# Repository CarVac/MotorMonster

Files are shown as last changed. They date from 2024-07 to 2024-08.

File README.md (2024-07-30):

# MotorMonster

MotorMonster is intended to be a 5x TMC2160 stepper driver board for 3D printers and other applications, that is actually designed to properly drive the optimal currents for high performance NEMA 17 motors: just north of 2.8 amps RMS.

Many existing 3D printer boards use improper sense resistors.
The BTT SKR Pico, for example, has a limit of 1.4 amps RMS due to its high sense resistor values.
Conversely, the BTT Kraken overspecs its currents with extremely low sense resistors, leaving the TMC drivers starved for sense voltage resolution.

Other boards use StepStick drivers for modularity, but those have worse thermal dissipation than integrated drivers.

The goal of this project is to have a focused, single-board solution for high performance motor driving, leaving everything else to be left to a standard 3D printer motherboard.
With 5 drivers, it should be suitable for 4WD CoreXY + an extruder, or cross gantry + an extruder.

You can choose what sense resistors you want to tailor the board to your own needs.

The MCU is an RP2040, which may be a tad bit slow for the very fastest applications but it's a chip I have a lot of experience with, reducing development risk.

# Acknowledgements

The RP2040 and supporting circuitry is based on https://github.com/Armastardo/OpenRectangleTemplate

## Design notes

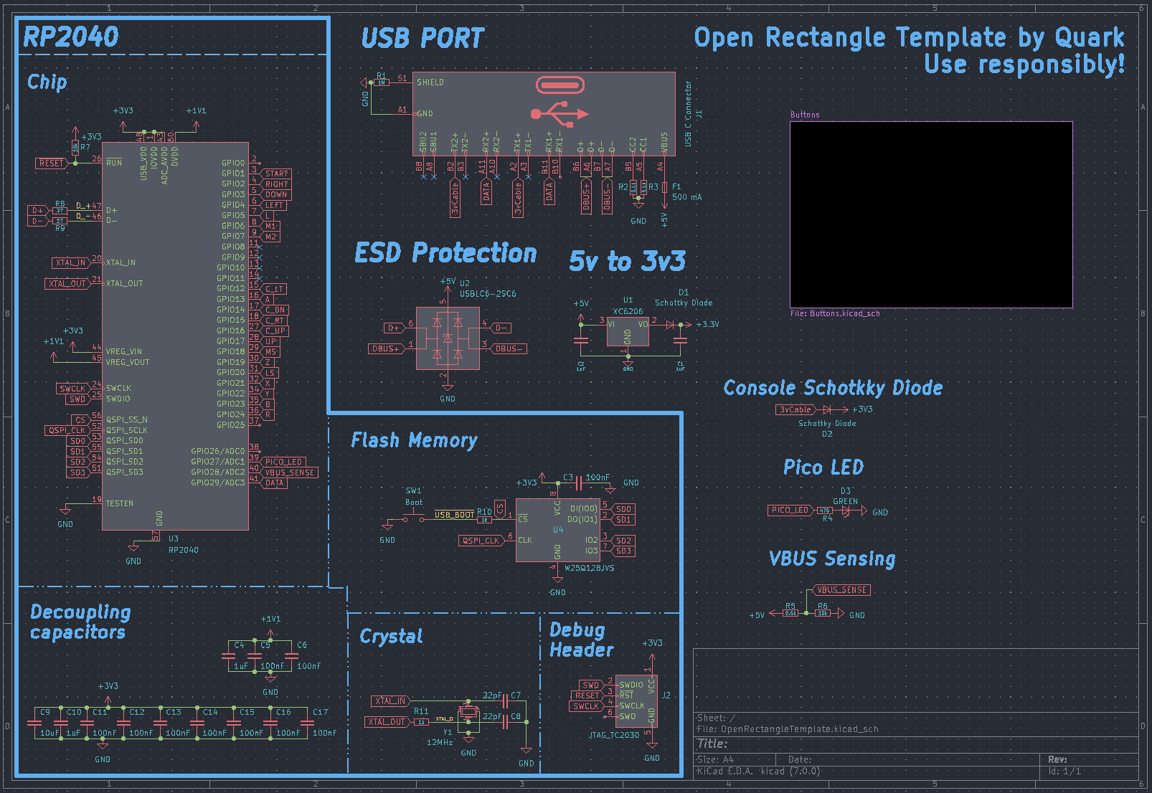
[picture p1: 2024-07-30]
MotorMonster/Pictures/Schematic.png

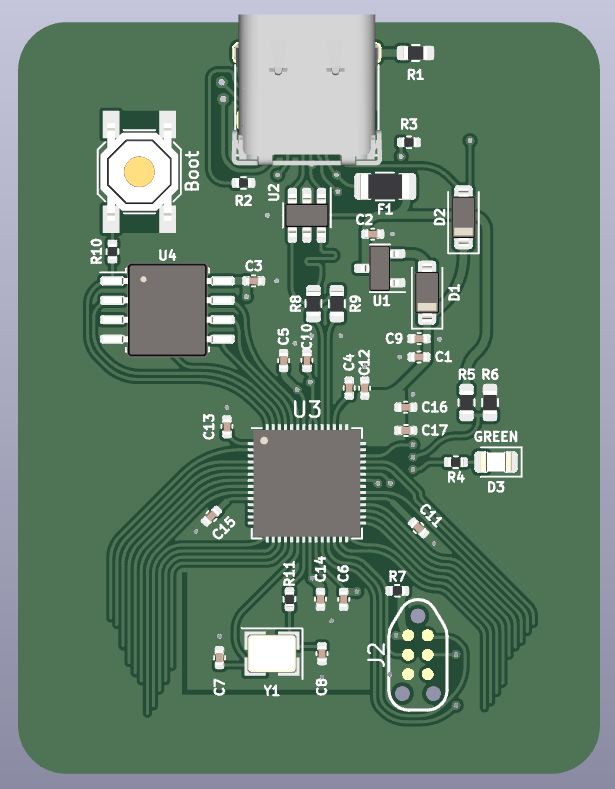
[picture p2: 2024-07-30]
MotorMonster/Pictures/KicadRender.png

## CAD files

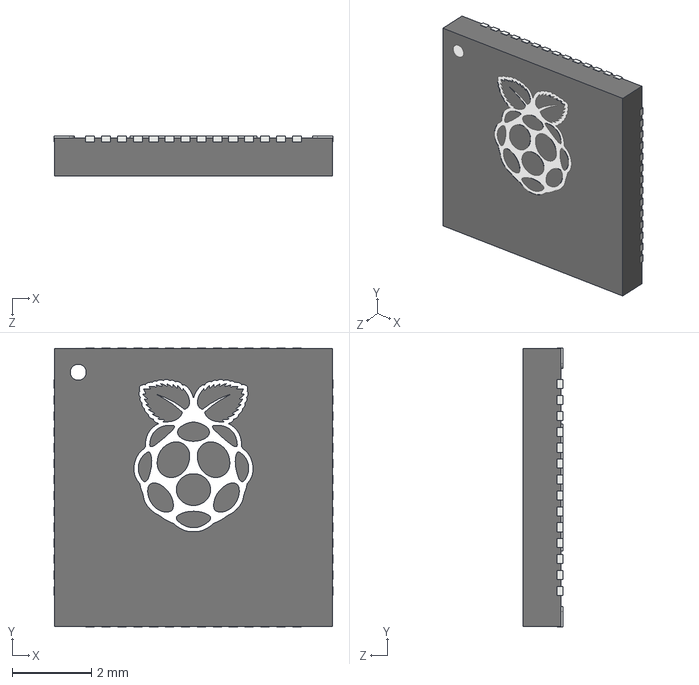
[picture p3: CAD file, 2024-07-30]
MotorMonster/model/RP2040_QFN_PACKAGE.STEP
7.02 x 7.02 x 1.00 mm

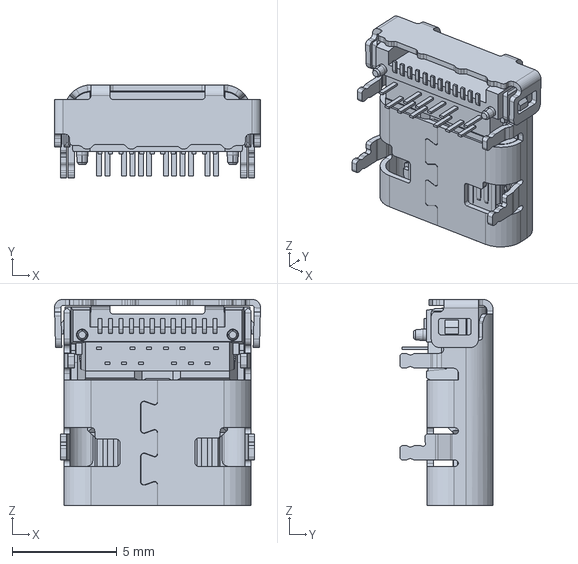
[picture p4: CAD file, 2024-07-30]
MotorMonster/model/2171830001.stp
9.85 x 4.46 x 9.87 mm

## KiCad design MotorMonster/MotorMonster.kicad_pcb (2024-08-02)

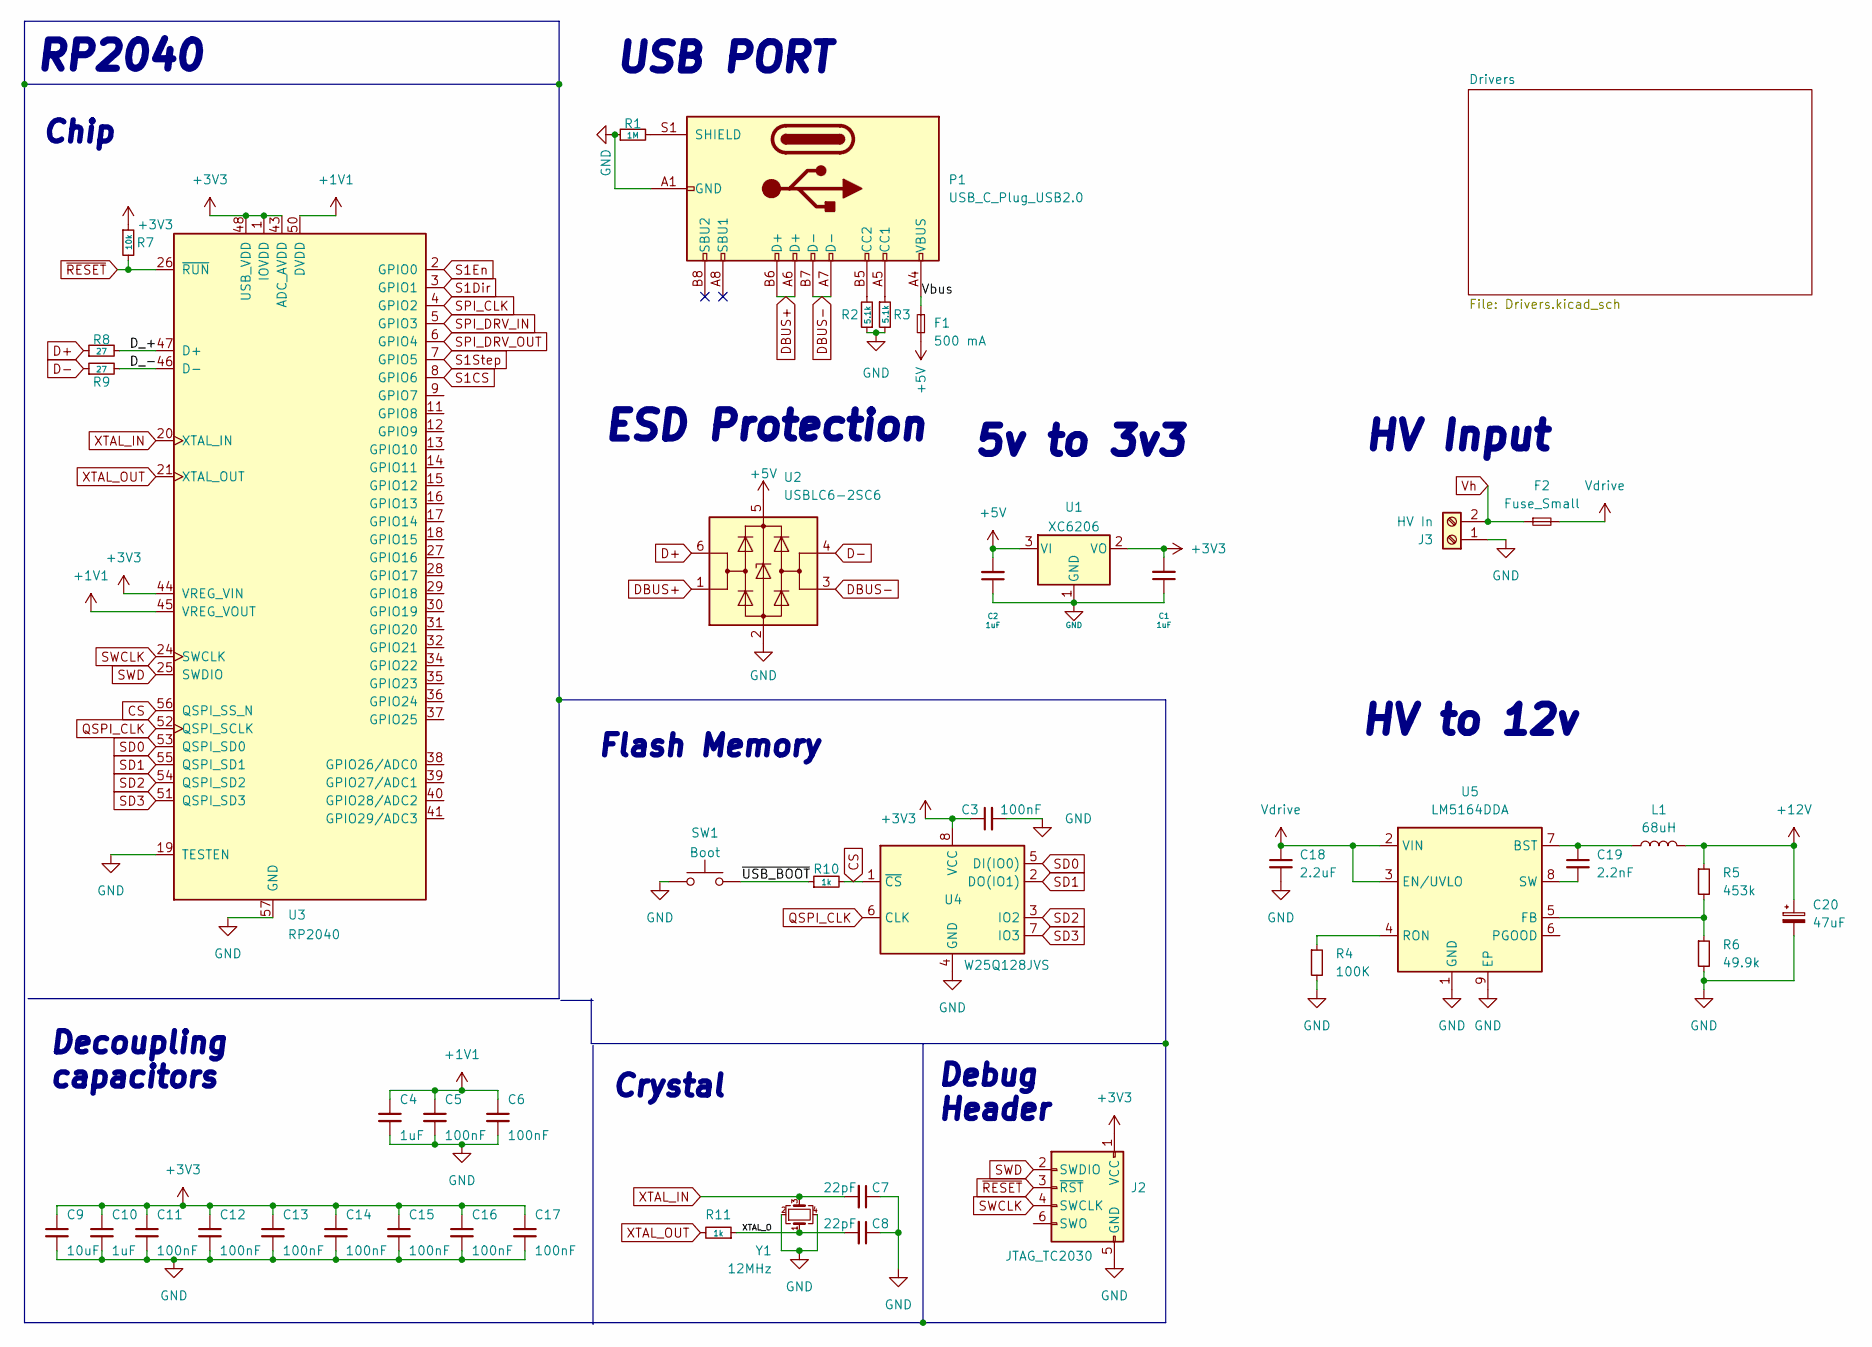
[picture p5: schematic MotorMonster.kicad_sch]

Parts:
C1, C2, C4, C10: 1uF; C_0402_1005Metric; LCSC C52923
C3, C5, C6, C11, C12, C13, C14, C15, C16, C17: 100nF; C_0402_1005Metric; LCSC C1525
C7, C8: 22pF; C_0402_1005Metric; LCSC C1555
C9: 10uF; C_0402_1005Metric; LCSC C15525
C18: 2.2uF; C_1206_3216Metric_Pad1.33x1.80mm_HandSolder; LCSC C170101
C19: 2.2nF; C_0603_1608Metric_Pad1.08x0.95mm_HandSolder; LCSC C113804
C20: 47uF; C_1206_3216Metric_Pad1.33x1.80mm_HandSolder; LCSC C403725
F1: 500 mA; Fuse_1206_3216Metric; LCSC C70076
F2: Fuse_Small; Fuseholder_Clip-6.3x32mm_Littelfuse_122_Inline_P34.21x7.62m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
J2: JTAG_TC2030; CON_TC2030_outlined
J3: HV In; TerminalBlock_Altech_AK300-2_P5.00mm
L1: 68uH; L_12x12mm_H8mm; LCSC C2929504
P1: USB_C_Plug_USB2.0; USB_C_Receptacle_G-Switch_GT-USB-7010ASV; LCSC C2988369
R1: 1M; R_0603_1608Metric; LCSC C22935
R2, R3: 5.1k; R_0402_1005Metric; LCSC C25905
R4: 100K; R_0402_1005Metric_Pad0.72x0.64mm_HandSolder; LCSC C217682
R5: 453k; R_0402_1005Metric_Pad0.72x0.64mm_HandSolder; LCSC C27009
R6: 49.9k; R_0402_1005Metric_Pad0.72x0.64mm_HandSolder; LCSC C25897
R7: 10k; R_0402_1005Metric; LCSC C25744
R8, R9: 27; R_0603_1608Metric; LCSC C25190
R10, R11: 1k; R_0402_1005Metric; LCSC C11702
SW1: Boot; SW_SPST_SKQG_WithStem; LCSC C318884
U1: XC6206; SOT-23; LCSC C5446
U2: USBLC6-2SC6; SOT-23-6; LCSC C7519
U3: RP2040; RP2040-QFN-56; LCSC C2040
U4: W25Q128JVS; SOIC-8_5.23x5.23mm_P1.27mm; LCSC C97521
U5: LM5164DDA; HSOP-8-1EP_3.9x4.9mm_P1.27mm_EP2.41x3.1mm_ThermalVias; LCSC C477928
Y1: 12MHz; Crystal_SMD_3225-4Pin_3.2x2.5mm; LCSC C9002

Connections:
+1V1: C4.1, C5.1, C6.1, U3.23 (DVDD), U3.45 (VREG_VOUT), U3.50 (DVDD)
+3V3: C1.2, C3.1, C9.1, C10.1, C11.1, C12.1, C13.1, C14.1, C15.1, C16.1, C17.1, J2.1 (VCC), R7.1, U1.2 (VO), U3.1 (IOVDD), U3.10 (IOVDD), U3.22 (IOVDD), U3.33 (IOVDD), U3.42 (IOVDD), U3.43 (ADC_AVDD), U3.44 (VREG_VIN), U3.48 (USB_VDD), U3.49 (IOVDD), U4.8 (VCC); also elsewhere on the board
+5V: C2.2, F1.2, U1.3 (VI), U2.5 (VBUS)
+12V: C20.1, L1.2, R5.1; also elsewhere on the board
/D_+: R8.2, U3.47 (D+)
/D_-: R9.2, U3.46 (D-)
/Vbus: F1.1, P1.A4 (VBUS), P1.A9 (VBUS), P1.B4 (VBUS), P1.B9 (VBUS)
/XTAL_O: C8.2, R11.1, Y1.1
/~USB_BOOT: R10.1, SW1.2
CS: R10.2, U3.56 (QSPI_SS_N), U4.1 (~CS)
D+: R8.1, U2.6 (I/O1)
D-: R9.1, U2.4 (I/O2)
DBUS+: P1.A6 (D+), P1.B6 (D+), U2.1 (I/O1)
DBUS-: P1.A7 (D-), P1.B7 (D-), U2.3 (I/O2)
GND: C1.1, C2.1, C3.2, C4.2, C5.2, C6.2, C7.1, C8.1, C9.2, C10.2, C11.2, C12.2, C13.2, C14.2, C15.2, C16.2, C17.2, C18.2, C20.2, J2.5 (GND), J3.1, P1.A1 (GND), P1.A12 (GND), P1.B1 (GND), P1.B12 (GND), R1.1, R2.1, R3.2, R4.2, R6.2, SW1.1, U1.1 (GND), U2.2 (GND), U3.19 (TESTEN), U3.57 (GND), U4.4 (GND), U5.1 (GND), U5.9 (EP), Y1.2, Y1.4; also elsewhere on the board
unnamed: P1.A5 (CC1), R3.1
unnamed: P1.B5 (CC2), R2.2
unnamed: P1.S1 (SHIELD), R1.2
unnamed: C19.1, L1.1, U5.7 (BST)
unnamed: R5.2, R6.1, U5.5 (FB)
unnamed: R4.1, U5.4 (RON)
unnamed: C19.2, U5.8 (SW)
QSPI_CLK: U3.52 (QSPI_SCLK), U4.6 (CLK)
S1CS: U3.8 (GPIO6); also elsewhere on the board
S1Dir: U3.3 (GPIO1); also elsewhere on the board
S1En: U3.2 (GPIO0); also elsewhere on the board
S1Step: U3.7 (GPIO5); also elsewhere on the board
SD0: U3.53 (QSPI_SD0), U4.5 (DI(IO0))
SD1: U3.55 (QSPI_SD1), U4.2 (DO(IO1))
SD2: U3.54 (QSPI_SD2), U4.3 (IO2)
SD3: U3.51 (QSPI_SD3), U4.7 (IO3)
SPI_CLK: U3.4 (GPIO2); also elsewhere on the board
SPI_DRV_IN: U3.5 (GPIO3); also elsewhere on the board
SPI_DRV_OUT: U3.6 (GPIO4); also elsewhere on the board
SWCLK: J2.4 (SWCLK), U3.24 (SWCLK)
SWD: J2.2 (SWDIO), U3.25 (SWDIO)
Vdrive: C18.1, F2.2, U5.2 (VIN), U5.3 (EN/UVLO); also elsewhere on the board
Vh: F2.1, J3.2
XTAL_IN: C7.2, U3.20 (XTAL_IN), Y1.3
XTAL_OUT: R11.2, U3.21 (XTAL_OUT)
~RESET: J2.3 (~RST), R7.2, U3.26 (~RUN)

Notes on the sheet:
Crystal
USB PORT
HV Input
Flash Memory
HV to 12v
RP2040
Debug Header
Chip
5v to 3v3
ESD Protection
Decoupling capacitors

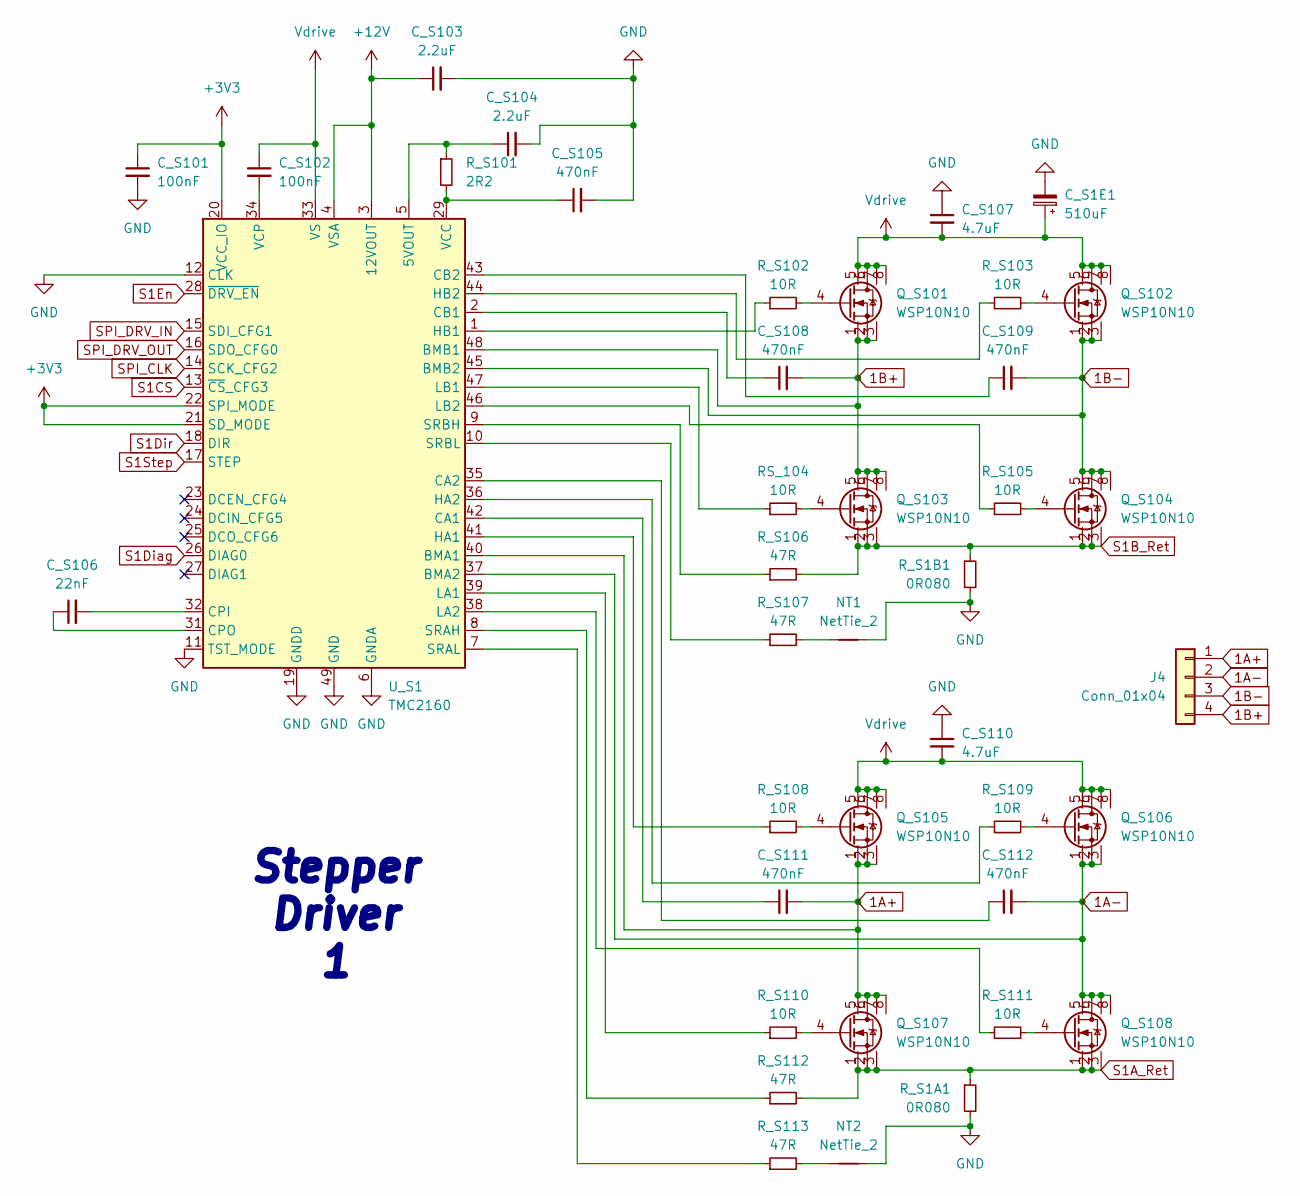
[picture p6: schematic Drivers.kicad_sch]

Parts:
C_S1E1: 510uF; CP_Radial_D18.0mm_P7.50mm
C_S101: 100nF; C_0402_1005Metric_Pad0.74x0.62mm_HandSolder; LCSC C1525
C_S102: 100nF; C_0402_1005Metric_Pad0.74x0.62mm_HandSolder; LCSC C162178
C_S103, C_S104: 2.2uF; C_0603_1608Metric_Pad1.08x0.95mm_HandSolder; LCSC C57895
C_S105, C_S108, C_S109, C_S111, C_S112: 470nF; C_1206_3216Metric_Pad1.33x1.80mm_HandSolder; LCSC C313105
C_S106: 22nF; C_0603_1608Metric_Pad1.08x0.95mm_HandSolder; LCSC C313105
C_S107, C_S110: 4.7uF; C_1210_3225Metric_Pad1.33x2.70mm_HandSolder; LCSC C2979983
J4: Conn_01x04; JST_XH_B4B-XH-A_1x04_P2.50mm_Vertical
NT1, NT2: NetTie_2; NetTie-2_SMD_Pad0.5mm
Q_S101, Q_S102, Q_S103, Q_S104, Q_S105, Q_S106, Q_S107, Q_S108: WSP10N10; SOIC-8_3.9x4.9mm_P1.27mm; LCSC C2827250
RS_104: 10R; R_0402_1005Metric_Pad0.72x0.64mm_HandSolder; LCSC C284283
R_S1A1, R_S1B1: 0R080; R_2512_6332Metric_Pad1.40x3.35mm_HandSolder; LCSC C5154744
R_S101: 2R2; R_0603_1608Metric_Pad0.98x0.95mm_HandSolder; LCSC C861308
R_S102, R_S103, R_S105, R_S108, R_S109, R_S110, R_S111: 10R; R_0402_1005Metric_Pad0.72x0.64mm_HandSolder; LCSC C284283
R_S106, R_S107, R_S112, R_S113: 47R; R_0402_1005Metric_Pad0.72x0.64mm_HandSolder; LCSC C284589
U_S1: TMC2160; TQFP-48-1EP_7x7mm_P0.5mm_EP5x5mm; LCSC C465948

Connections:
1A+: C_S111.2, J4.1, Q_S105.1 (D), Q_S105.2 (G), Q_S105.3 (S), Q_S107.5, Q_S107.6, Q_S107.7, Q_S107.8, U_S1.40 (BMA1)
1A-: C_S112.2, J4.2, Q_S106.1 (D), Q_S106.2 (G), Q_S106.3 (S), Q_S108.5, Q_S108.6, Q_S108.7, Q_S108.8, U_S1.37 (BMA2)
1B+: C_S108.2, J4.4, Q_S101.1 (D), Q_S101.2 (G), Q_S101.3 (S), Q_S103.5, Q_S103.6, Q_S103.7, Q_S103.8, U_S1.48 (BMB1)
1B-: C_S109.2, J4.3, Q_S102.1 (D), Q_S102.2 (G), Q_S102.3 (S), Q_S104.5, Q_S104.6, Q_S104.7, Q_S104.8, U_S1.45 (BMB2)
+3V3: C_S101.1, U_S1.20 (VCC_IO), U_S1.21 (SD_MODE), U_S1.22 (SPI_MODE); also elsewhere on the board
+12V: C_S103.1, U_S1.3 (12VOUT), U_S1.4 (VSA); also elsewhere on the board
GND: C_S1E1.2, C_S101.2, C_S103.2, C_S104.2, C_S105.2, C_S107.1, C_S110.1, NT1.2, NT2.2, R_S1A1.2, R_S1B1.2, U_S1.6 (GNDA), U_S1.11 (TST_MODE), U_S1.12 (CLK), U_S1.19 (GNDD), U_S1.30 (GNDD), U_S1.49 (GND); also elsewhere on the board
unnamed: NT1.1, R_S107.2
unnamed: NT2.1, R_S113.2
unnamed: Q_S101.4, R_S102.2
unnamed: Q_S102.4, R_S103.2
unnamed: Q_S103.4, RS_104.2
unnamed: Q_S104.4, R_S105.2
unnamed: Q_S105.4, R_S108.2
unnamed: Q_S106.4, R_S109.2
unnamed: Q_S107.4, R_S110.2
unnamed: Q_S108.4, R_S111.2
unnamed: C_S104.1, R_S101.1, U_S1.5 (5VOUT)
unnamed: C_S111.1, U_S1.42 (CA1)
unnamed: C_S112.1, U_S1.35 (CA2)
unnamed: C_S108.1, U_S1.2 (CB1)
unnamed: C_S109.1, U_S1.43 (CB2)
unnamed: C_S106.2, U_S1.32 (CPI)
unnamed: C_S106.1, U_S1.31 (CPO)
unnamed: R_S108.1, U_S1.41 (HA1)
unnamed: R_S109.1, U_S1.36 (HA2)
unnamed: R_S102.1, U_S1.1 (HB1)
unnamed: R_S103.1, U_S1.44 (HB2)
unnamed: R_S110.1, U_S1.39 (LA1)
unnamed: R_S111.1, U_S1.38 (LA2)
unnamed: RS_104.1, U_S1.47 (LB1)
unnamed: R_S105.1, U_S1.46 (LB2)
unnamed: R_S112.1, U_S1.8 (SRAH)
unnamed: R_S113.1, U_S1.7 (SRAL)
unnamed: R_S106.1, U_S1.9 (SRBH)
unnamed: R_S107.1, U_S1.10 (SRBL)
unnamed: C_S105.1, R_S101.2, U_S1.29 (VCC)
unnamed: C_S102.2, U_S1.34 (VCP)
S1A_Ret: Q_S107.1 (D), Q_S107.2 (G), Q_S107.3 (S), Q_S108.1 (D), Q_S108.2 (G), Q_S108.3 (S), R_S1A1.1, R_S112.2
S1B_Ret: Q_S103.1 (D), Q_S103.2 (G), Q_S103.3 (S), Q_S104.1 (D), Q_S104.2 (G), Q_S104.3 (S), R_S1B1.1, R_S106.2
S1CS: U_S1.13 (~CS_CFG3); also elsewhere on the board
S1Diag: U_S1.26 (DIAG0)
S1Dir: U_S1.18 (DIR); also elsewhere on the board
S1En: U_S1.28 (~DRV_EN); also elsewhere on the board
S1Step: U_S1.17 (STEP); also elsewhere on the board
SPI_CLK: U_S1.14 (SCK_CFG2); also elsewhere on the board
SPI_DRV_IN: U_S1.15 (SDI_CFG1); also elsewhere on the board
SPI_DRV_OUT: U_S1.16 (SDO_CFG0); also elsewhere on the board
Vdrive: C_S1E1.1, C_S102.1, C_S107.2, C_S110.2, Q_S101.5, Q_S101.6, Q_S101.7, Q_S101.8, Q_S102.5, Q_S102.6, Q_S102.7, Q_S102.8, Q_S105.5, Q_S105.6, Q_S105.7, Q_S105.8, Q_S106.5, Q_S106.6, Q_S106.7, Q_S106.8, U_S1.33 (VS); also elsewhere on the board

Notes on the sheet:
Stepper Driver 1

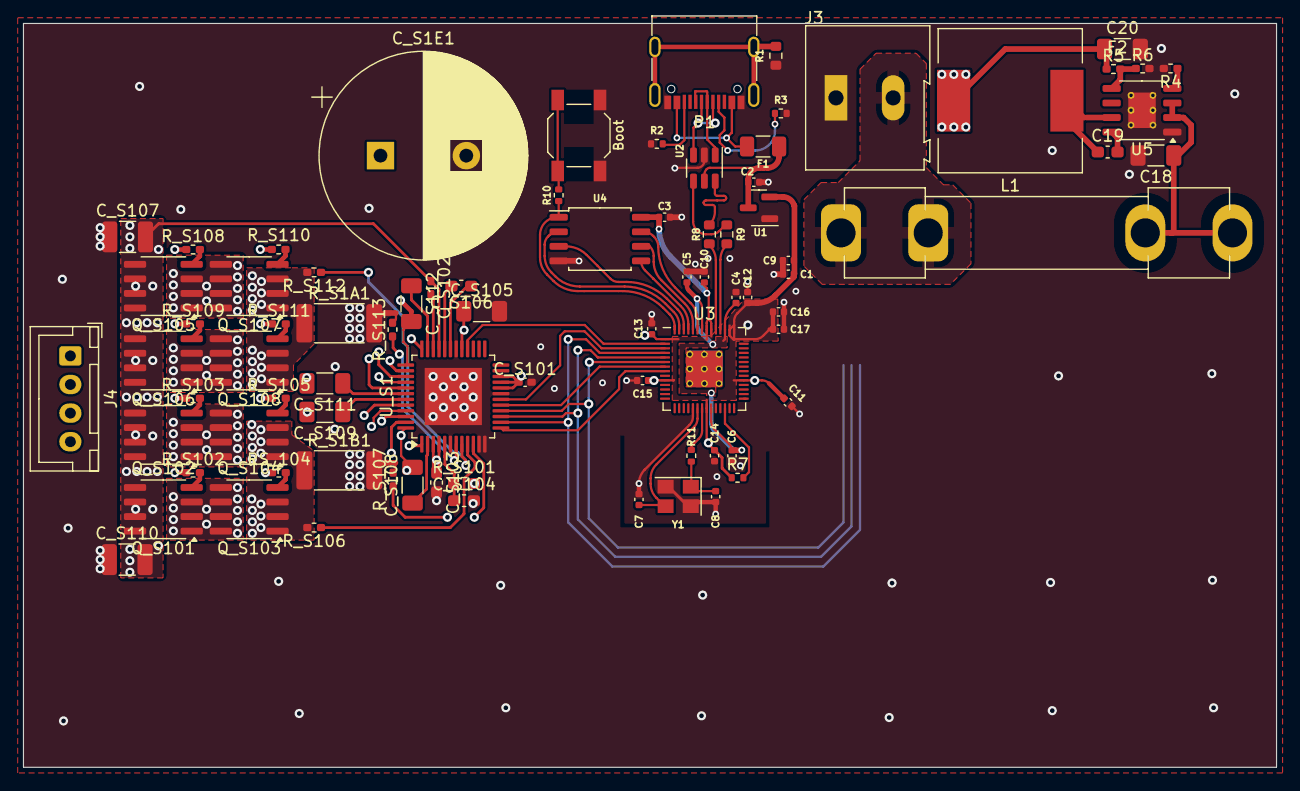
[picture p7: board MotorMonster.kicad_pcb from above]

Board: 4 copper layers, 109.5 x 65.0 mm, 83 parts (0 on the bottom side), 76 nets.

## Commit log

2024-07-30 mention that the sense resistors can be changed
2024-07-31 basic layout and some routing done
    [Drivers.kicad_sch, MotorMonster.kicad_pcb, MotorMonster.kicad_sch]
2024-08-02 fully laid out
    [Drivers.kicad_sch, MotorMonster.kicad_pcb, MotorMonster.kicad_sch]
